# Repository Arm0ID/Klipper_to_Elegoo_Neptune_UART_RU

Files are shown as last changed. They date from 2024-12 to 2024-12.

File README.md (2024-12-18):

# Klipper_to_Elegoo_Neptune_UART_RU

## [Описание]
В данном репозитории я попробую подробно описать как скомпилировать прошивку и подключить 3D принтер **Elegoo Neptune 3 Pro** по протоколу *UART* (не используя USB кабель) в прошивке *Klipper*, которая установлена на одноплатник **BTT Pi**, а так же разместить железки в корпусе.
Рекомендую сначала прочитать до конца, чтобы сложилась общая картинка.
## [Содержание]
0. Предусловие
1. Сборка и Компиляция прошивки
2. Прошивка принтера
3. Подключение железок
4. Подстройка Klipper

## [Приступим]
### 0. Предусловие
Инструкция рассчитана на то, что Вы уже установили **Klipper** на свой одноплатный компьютер и загрузили конфигурационный файл(***printer.cfg***) для своего принтера.
Если же нет, то найти инструкцию можно [тут](https://github.com/Konstant-3d/Neptune3pro-klipper/wiki/%D0%9F%D1%80%D0%BE%D1%81%D1%82%D0%BE%D0%B9-%D0%B3%D0%B0%D0%B9%D0%B4-%D0%BF%D0%BE-%D1%83%D1%81%D1%82%D0%B0%D0%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), но на этапе прошивки принтера можно остановиться и вернуться сюда.
Эта инструкция также подойдет для другого одноплатника, нужно будет гуглить *pinout*.

*Хотелось бы отметить, что у меня все заработало спустя три перезагрузки.* 

#### *Мой конфиг*:
* Принтер Neptune 3Pro
* Одноплатник BTT Pi
#### *Вам понадобится*:
* *СД*-карта для прошивки принтера
* Соединительные провода:
	* F-M 3штуки 10-15см
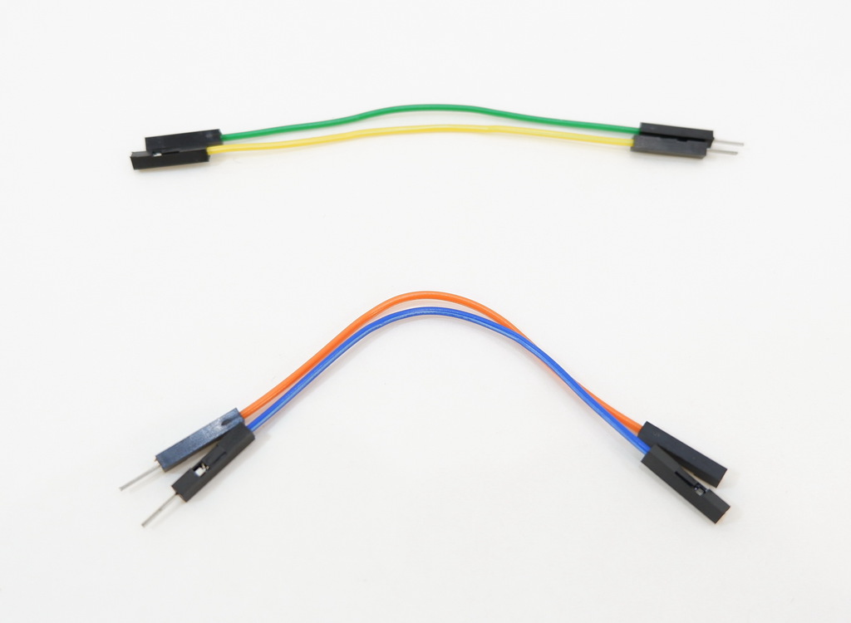
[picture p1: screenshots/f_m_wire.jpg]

* *SSH*-клиент(например *Putty*, но я буду пользоваться *PowerShell*)

### 1. Сборка и компиляция прошивки

#### 1.1 Подключаемся к BTT Pi по SSH 
Я буду использовать *PowerShell*, поэтому после открытия пишу команду:
```bash
ssh biqu@192.168.0.161
```
*где:* 
* `biqu` - имя стандартного пользователя в *BTT-CB1*,
* `192.168.0.161` - адрес одноплатника в локальной сети.

Далее он запросит пароль, который тоже `biqu` - и мы подключились, будет выведен некий логотип платы/ОС.
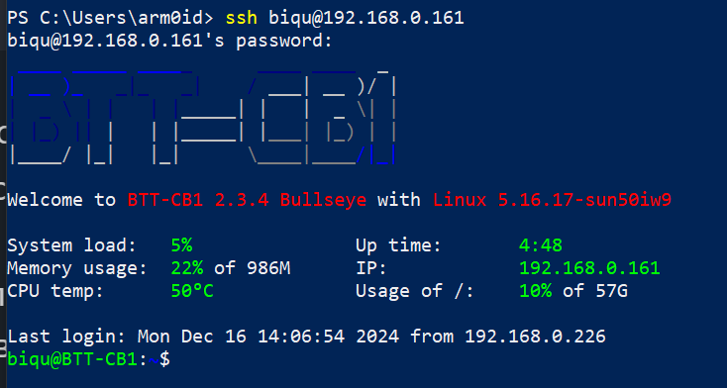
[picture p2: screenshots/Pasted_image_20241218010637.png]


#### 1.2 Собираем прошивку под UART в BIN-арник
Теперь нас ждет этап сборки/компиляции прошивки, который будет исполнять сам *linux* - это нужно, чтобы у нас не было потом ошибки `mcu protol error`, которая высвечивается на главной странице, когда версии *Klipper*-а и *mcu*(платы принтера) не совпадают.
  1. Перейдем в каталог `klipper`:
```bash
cd klipper
```
  2. Очистим каталог от предыдущих компиляций, если такие были:
```bash
make clean
```
  3. Запустим конфигуратор прошивки:
```bash
make menuconfig
```
  4. Настроим конфигуратор:
		Разные версии Klipper-а будут слегка отличаться, но основные пункты останутся:

> [ * ] Enable extra low-level configuration options
> 
> - **Micro-controller Architecture**: STMicroelectronics STM32
> - **Processor model**: STM32F401
> - **Bootloader offset**: 32Kib bootloader
> - **Clock Reference**: 8 MHz crystal
> - **Communication interface**: Serial (on USART2 PA3/PA2)
> - **Baud rate for serial port**: 250000
> - **GPIO pins to set at micro-controller startup**

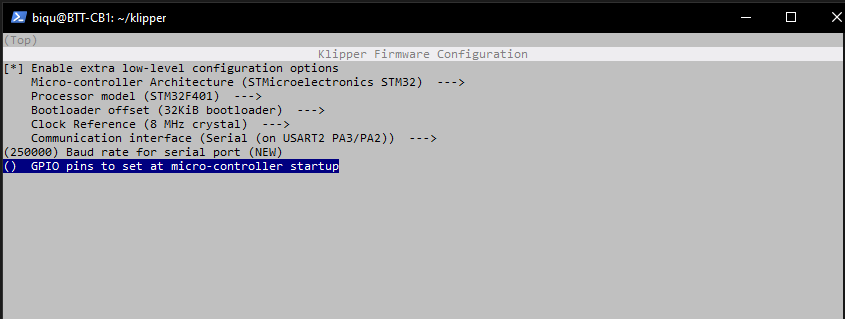
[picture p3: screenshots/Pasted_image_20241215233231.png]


5. Сохраним и соберем прошивку:
	* После того, как Вы настроили *конфигуратор* нужно будет выйти, сохранив изменения: нажимаем `Q` и `Y`.
	* Чтобы преобразовать это в BIN-арник для принтера нужно будет вписать в консоль:
```bash
 make
```


*Если вы увидели такое сообщение, то можно продолжать. Версия может быть другой.*

6. Закроем SSH подключение:
```bash
exit
```
### 2. Прошивка принтера 
Для прошивки принтера нужно, чтобы вывод утилиты *make*, а именно *klipper.bin* оказался на СД-карте и в принтере:
#### 2.1.1 Скачаем прошивку на ПК - Способ I:
```bash
scp biqu@192.168.0.161:~/klipper/out/klipper.bin e:\prog\klipper_n3pro
```
*где:*
* *scp* - утилита для безопасного копирования данных между Linux-системами по протоколу *SSH*,
* *biqu* - стандартное имя пользователя *BTT-CB1*,
* *192.168.0.161* - локальный адрес одноплатника,
* *~/klipper/out/klipper.bin* - стандартный адрес, куда сохраняет *make*,
* *e:\prog\klipper_n3pro* - путь на моем ПК, куда я скачал прошивку.

#### 2.1.2 Скачаем прошивку на ПК - Способ II(Если нет `scp`):

Если не получилось первым способом, можно воспользоваться программой [WinSCP](https://winscp.net/eng/download.php)
* После установки и открытия программы нужно будет настроить подключение, вписав локальный адрес, логи и пароль; выбрав 22 и метод подключения SCP:
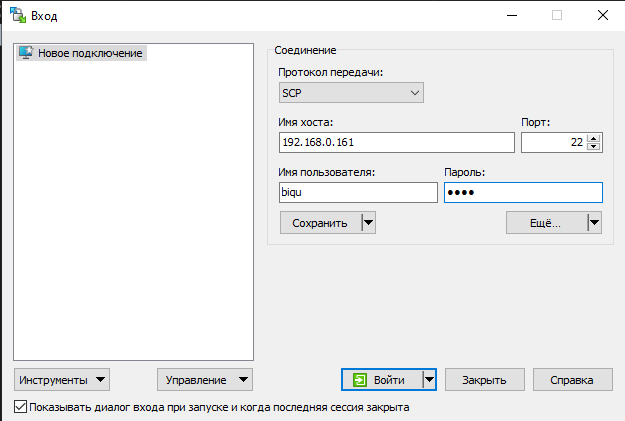
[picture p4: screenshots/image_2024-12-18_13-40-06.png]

* Переходим по пути к собранному BIN-арнику в правом окне: `/home/biqu/klipper/out/`
* В левом окне открываем путь куда мы хотим скачать
* Нажимаем ПКМ по файлику `klipper.bin` и выбираем `Получить` в контекстном меню.
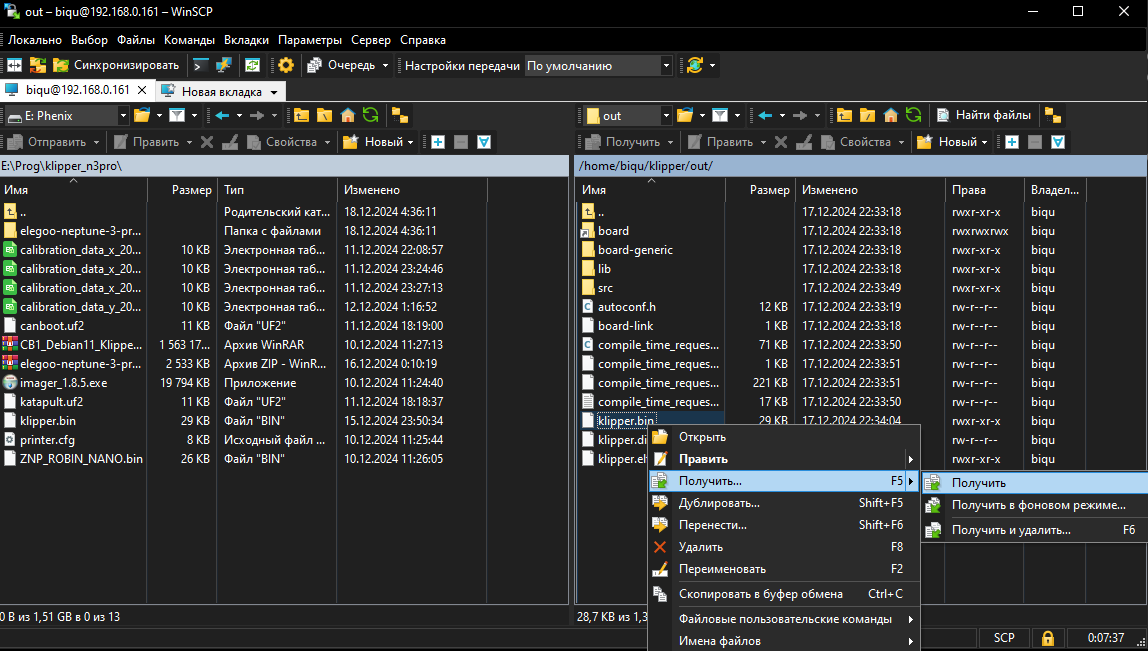
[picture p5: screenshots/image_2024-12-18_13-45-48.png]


#### 2.2 Подготовка СД-карты
	1. Прежде чем копировать *BIN*-арник на карту памяти нужно его переименовать, иначе принтер проигнорирует его: `ZNP_ROBIN_NANO.bin`,
	2. Форматируем СД-карту в формат *FAT32*,
	3. Копируем `ZNP_ROBIN_NANO.bin` в корень карты.

#### 2.3 Прошивка принтера
	1. Выключаем питания принтера,
	2. Вставляем СД-карту в соответствующий разъем на принтере,
	3. Включаем принтер,
	4. Ждем в районе 5-10 минут,
	5. Выключаем питание и проверяем переименовался ли файл на СД-карте на `ZNP_ROBIN_NANO.CUR` - это сигнализирует о том, что принтер успешно прошился.

### 3. Подключаем принтер к одноплатнику по UART
На моей *BTT Pi* есть гребенка GPIO разъемов:
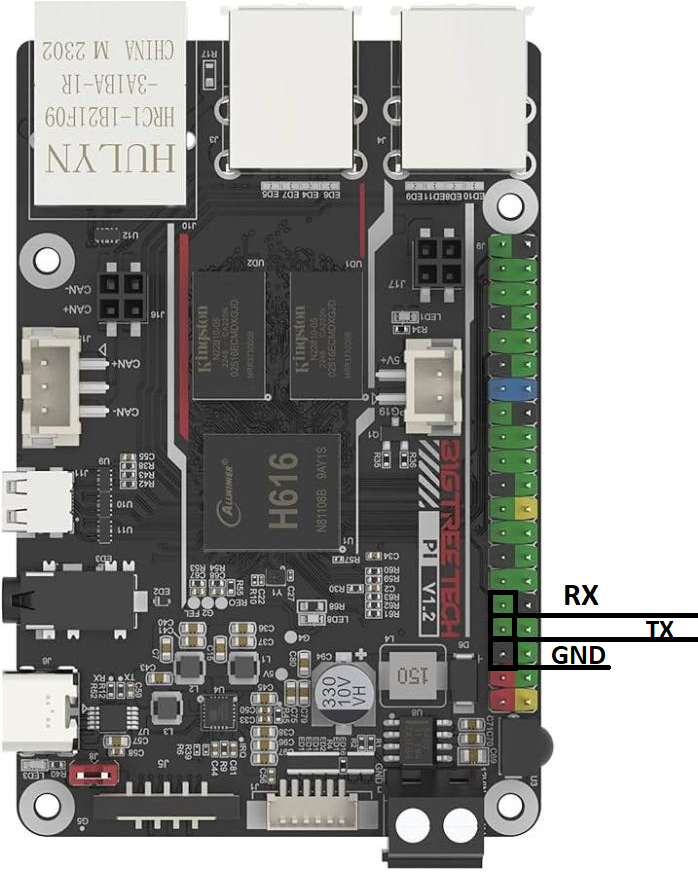
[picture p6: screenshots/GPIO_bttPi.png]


И на принтере разъем *J17*:
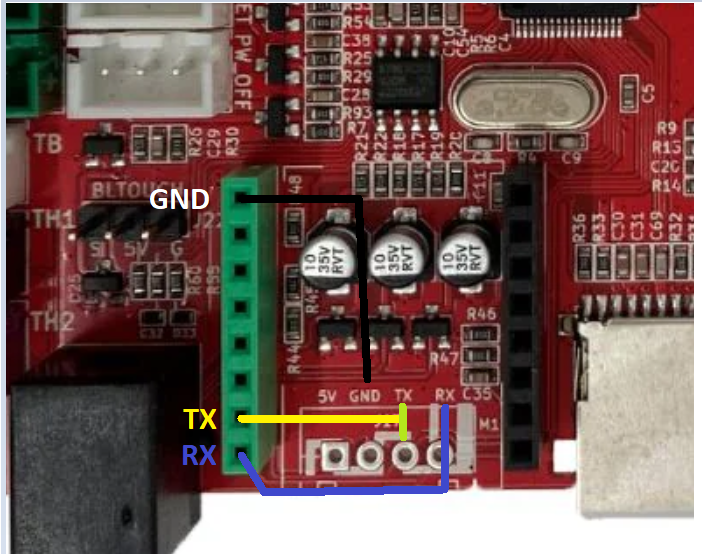
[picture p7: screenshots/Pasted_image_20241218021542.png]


А соединять нужно по принципу:

| Пины Robin Nano | Пины GPIO BTT Pi |
| --- | --- |
| *TX* | *RX* |
| *RX* | *TX* |
| *GND* | *GND* |

*я специально обвел контакты с разъема под ESP-модуль, чтобы можно было легко подключить соединительным проводом F-M(мама-папа) от Ардуино*

У меня получилось вот так:


Чтобы смонтировать внутри корпуса нужно:
1. заранее распечатать два файлика из папки `models`:
	* Stands - 3 штуки
	* base - 1 штука
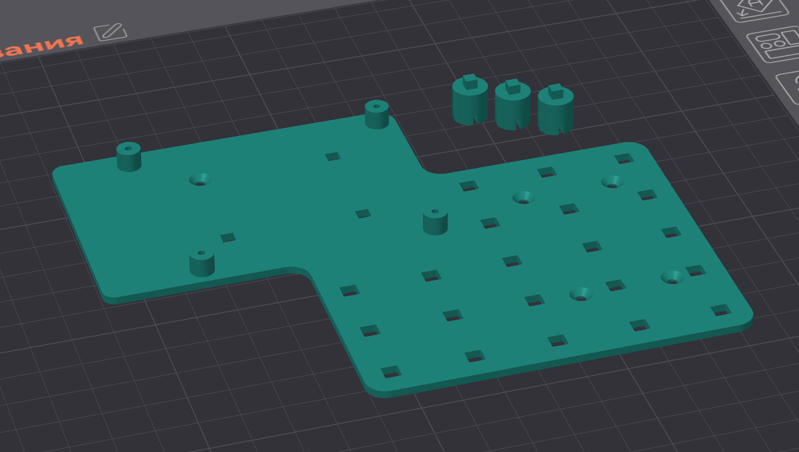
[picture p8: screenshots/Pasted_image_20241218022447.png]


2. Запастись 6 винтами и терпением, чтобы смонтировать пластину внутри корпуса:
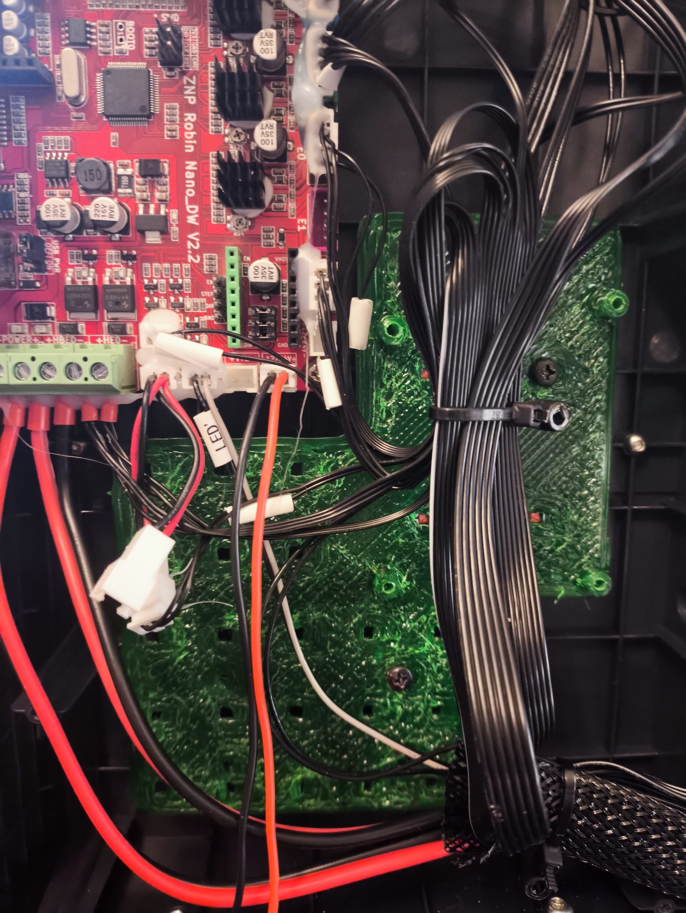
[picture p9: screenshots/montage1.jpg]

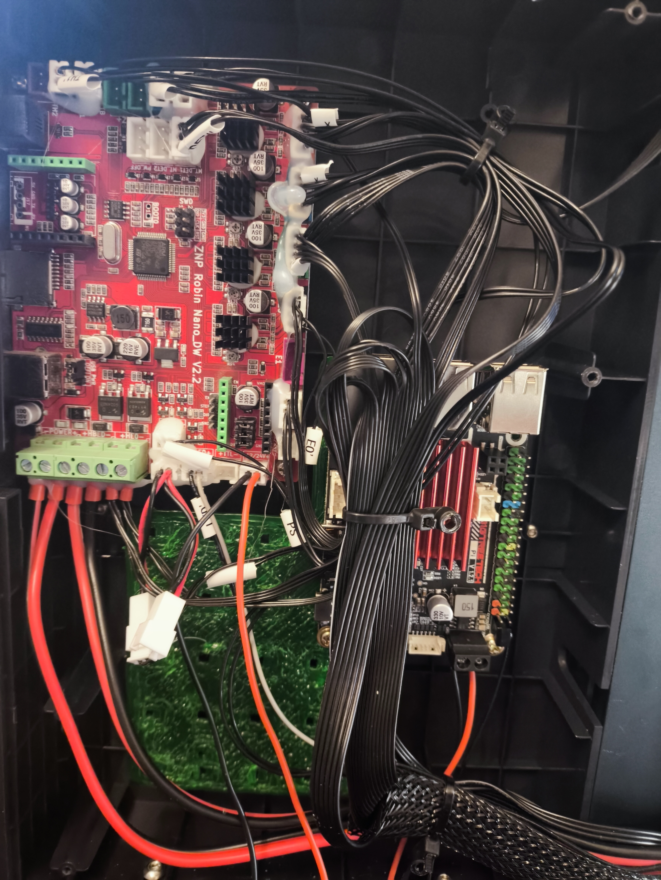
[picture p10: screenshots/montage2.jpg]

Штырьки нужны, чтобы закрепить переходную пластину на пересечениях ребер жесткости в пластике корпуса.
После монтажа всех компонентов можно закрутить крышку, а Wi-Fi антенну приклеить на балку вне корпуса.
* Питание для одноплатника я также взял с платы принтера - правый нижний разъем с маркировкой `-24V/+24V`.
### 4. Подстройка принтера
#### 4.1 Шаг первый
В самом интерфейсе Klipper нужно перейти в конфигурацию принтера - `printer.cfg` и заменить эту часть кода:
```cfg
[mcu]
serial: /dev/ttyUSB0
```
На:
```
[mcu]
serial: /dev/ttyS0
```
Сохранить и перезагрузить.
#### 4.2 Шаг второй - Способ I
Подключаемся по *SSH* к одноплатнику, как указано в п 1.1 и пишем команду:
```bash
sudo nano /boot/BoardEnv.txt
```
Открывается редактор текста, где нужно будет найти строку:
```BoardEnv.txt
console=display
```
и заменить ее на:
```BoardEnv.txt
console=serial
```
Затем нужно сохранить, выйти и перезагрузить:
1. Нажимаем `Ctrl` + `O`,
2. Нажимаем `Enter` - чтобы подтвердить,
3. Нажимаем `Ctrl` + `X` - чтобы выйти из редактора,
4. Пишем `reboot` - чтобы перезагрузить одноплатник.

#### 4.2 Шаг второй - Способ II(Если не сработал первый)
* Нужно будет выключить одноплатник,
* Достать СД-карту и подключить ее в Ваш ПК,
* Открываем раздел `boot`,
* Ищем там файлик `BoardEnv.txt` и открываем,
* Заменяем в нем `console=display` на `console=serial`,
* Сохраняем и **безопасно извлекаем** СД-карту,
* Возращаем на место в одноплатник,
* Включаем, радуемся.

## Источник

[Тык](https://www.printables.com/model/841472-elegoo-neptune-3-pro-klipper-upgrade-with-btt-pi-v)

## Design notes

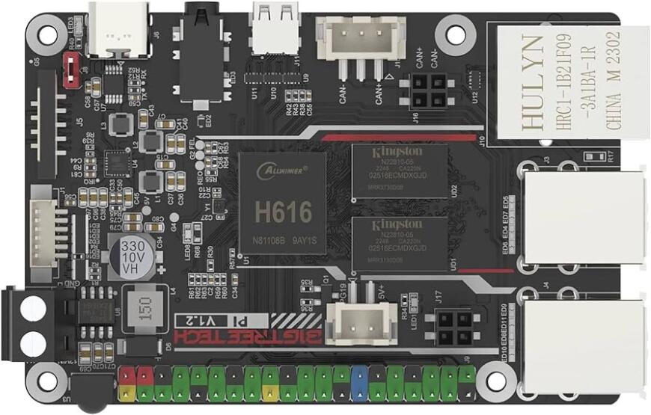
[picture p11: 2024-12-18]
screenshots/gpio_btt_pi.jpg

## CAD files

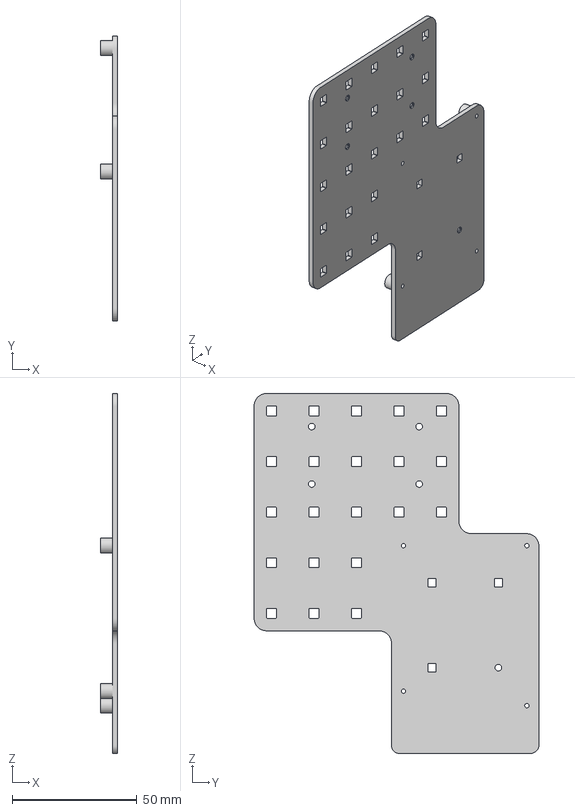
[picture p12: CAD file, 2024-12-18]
models/base.3mf
7.00 x 114.0 x 144.1 mm

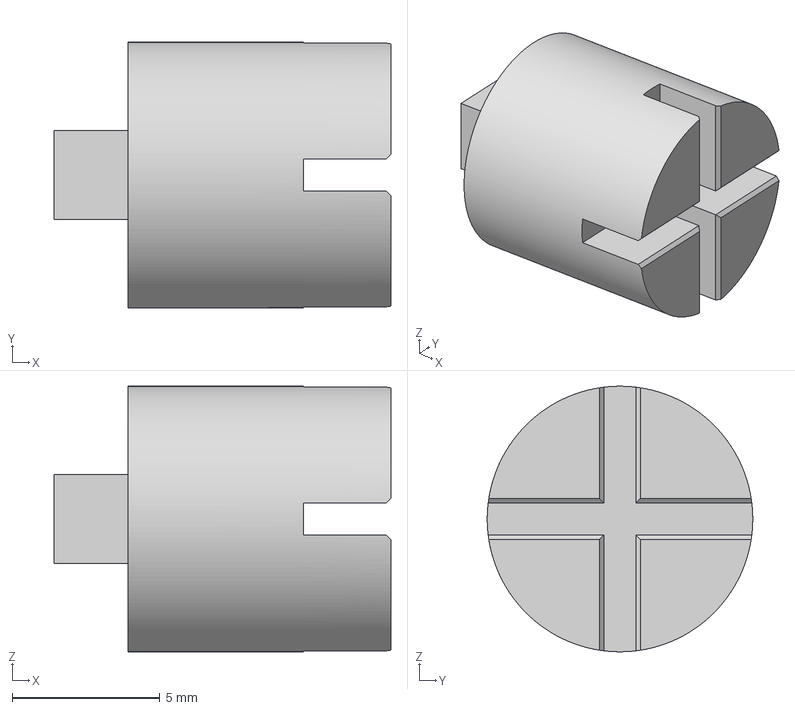
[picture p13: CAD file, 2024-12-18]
models/Stands.3mf
11.4 x 9.00 x 9.00 mm

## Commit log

2024-12-17 Предварительная запись
2024-12-18 Предварительная версия 2
2024-12-18 Предварительная версия 3
2024-12-18 Финальная 0.1
    [Stands.3mf, base.3mf]
2024-12-18 Стабильная v1?
2024-12-18 Финальная v2
